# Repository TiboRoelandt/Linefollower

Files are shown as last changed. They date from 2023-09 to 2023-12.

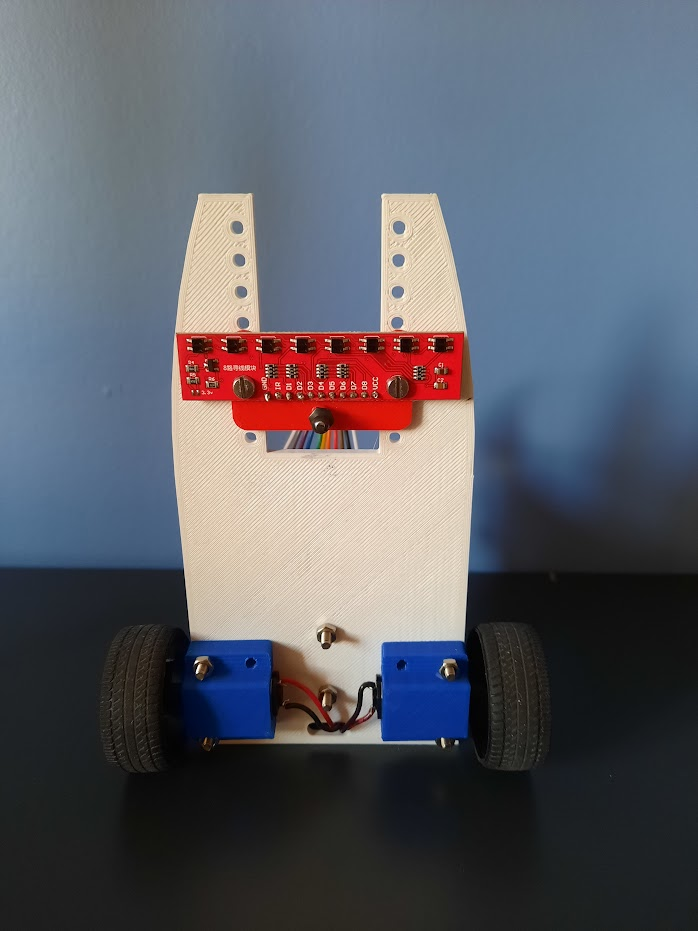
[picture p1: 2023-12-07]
images/LFC2.png

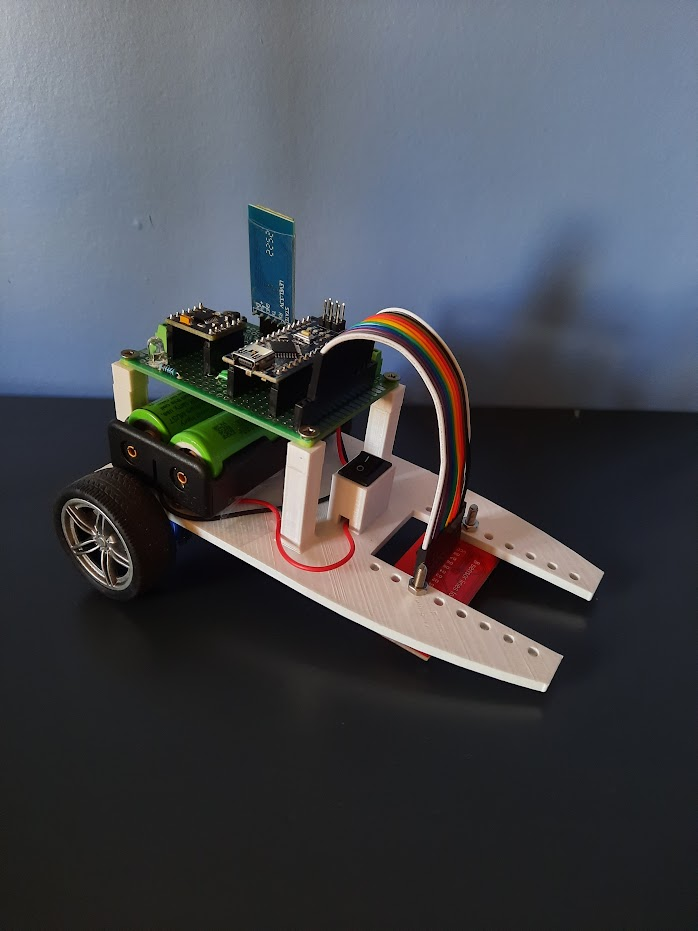
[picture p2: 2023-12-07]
images/LFC1.png

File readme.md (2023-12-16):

# LineFollower

lege repository die je als template kan gebruiken om een eigen repository te starten voor uw linefollower project



## specifications

microcontroller: ATmega328 (Arduino Nano)

motors: Metal Gear motor 6V-50:1

h-bridge: DRV8833

sensors: QTR-8A

batteries: 2x 18650 li-ion

wireless communication: HC-05

distance sensor - motors: 96mm 

weight: 245g

speed: 0,708 m/s

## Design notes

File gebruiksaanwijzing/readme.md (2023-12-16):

# Gebruiksaanwijzing

### opladen / vervangen batterijen
De batterijen die gebruikt worden zijn 2 18650 li-ion batterijen. Deze worden opgeladen met een geschikte oplader. Om de batterijen te vervangen moet eerst de PCB van de auto worden verwijderd. Hierna kunnen de batterijen uit de houder worden gehaald en opgeladen. 

### draadloze communicatie
#### verbinding maken
Voor de draadloze communicatie wordt er gebruik gemaakt van een HC-05 bluetooth module. Op de smartphone wordt de app "Serial Bluetooth Terminal" gebruikt om verbinding te maken met de module. Hiermee kunnen de commando's worden doorgestuurd naar de arduino. 

#### commando's
debug [on/off] => Opvragen van de ingestelde parrameters. 

run  => Starten van de LineFollower. 

stop => Stoppen van de LineFollower.  

set cycle [µs]  => Instellen van de cycle time. Deze is ongeveer het dubbele van de calculation time.

set power [0..255]  => Instellen van de power van de motoren. 

set diff [0..1]  => Door de diff aan te passen zal de auto vertragen of versnellen in de bochten. Hoe hoger diff hoe meer de auto versnelt in de bochten.

set kp [0..] => Dit is de corrigatie van de fout. Hoe hoger kp hoe sterker de auto zich corrigeert om de zwarte lijn in het midden van de sensor te hebben. Als deze te hoog is zal de auto schoken van links naar rechts over de lijn.

set ki [0..] => Hoe langer de error duurt hoe sterker de linfollower zal bijsturen. 

set kd [0..] => Dit is de foutverandering. Deze kijkt naar de fout uit de vorige cyclus en gaat dan de fout bijregelen. Was deze fout groot dan wordt er meer gecorigeerd.

calibrate black => Hierdoor worden de zwarte waarden van de sensor gecalibreert.  

calibrate white => Hierdoor worden de witte waarden van de sensor gecalibreert. 

### kalibratie
Het kalibreren van de senor gebeurd met de commando's "calibrate black" en "calibrate white". Om de zwarte waarden te kalibreren moet de sensor boven een zwart oppervlak staan en dan het commando ingeven. Om de witte waarden te kalibreren gebeurd het zelfde maar op een wit oppervlak. 

### settings
De robot rijdt stabiel met volgende parameters: cycle time: 3000, power: 75, diff: 0.75, kp:18, ki: 0.5, kd:0.4

### start/stop button
Er is een start/stop button voorzien op de robot. Deze bevindt zich op de PCB, de knop is aangesloten op een intterupt pin (pin2). Deze werkt met een intterupt functie en een debounce.

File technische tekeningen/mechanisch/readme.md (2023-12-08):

Assembly:



Base:


Sensor plaatje:



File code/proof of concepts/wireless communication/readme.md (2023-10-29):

# draadloze communicatie proof of concept
minimale hard- en software waarmee aangetoond wordt dat duplex kan gecommuniceerd worden tussen de microcontroller en een smartphone, gebruik makend van Arduino bluetooth controller.
<br />
### configuratie
HC-05
### opmerkingen
App: Arduino bluetooth controller
### gebruiksaanwijzing

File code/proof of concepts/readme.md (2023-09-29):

# Proof of Concepts

Een proof of concept is een combinatie van minimale hard- en software om eenvoudig aan te tonen dat iets werkt.  
Proof of concepts kunnen enerzijds als eerste poging dienen om een bepaald onderdeel van het project werkend te krijgen. Anderzijds kunnen ze tijdens het debuggen van het finale project dienen als test om eventuele hardware problemen te elimineren bij onduidelijke problemen.
<br />  
<br />
Een proof of concept bestaat uit
* een elektronisch schema (indien van toepassing)
* minimale code om de voorop gestelde zaken te demonstreren
* minimale uitleg / aandachtspunten
<br />
De elektronische schakelingen van de proof of concepts komen bij voorkeur overeen met deze van de uiteindelijke linefollower, zodat de code zonder aanpassingen op het finale project kan draaien.

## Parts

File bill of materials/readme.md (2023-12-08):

## bill of materials
<br />

|volgnummer|naam|omschrijving|nieuw/recup|kostprijs/stuk|aantal|subtotaal|
|---|----|---|---|---|---|---|
| 1|  Microcontroller | ATmega328P | Nieuw | €2,61 | 1 | €2,61 |
| 2|  Sensoren  | QTR-8A | Nieuw | €1,24 | 1 | €1,24 |
| 3| H-brug  | DRV8833 | Nieuw | €0,48 | 1 |  €0,48 |
| 4|  Motoren  | Gear motor 6V 50:1 | Nieuw | €3,25 | 2 | €6,5 |
| 5|  Bluetooth  | HC-05 module | Nieuw | €3,90 | 1 | €3,90 |
| 6|  Batterij  | 18650 | Recup | €0 | 1 | €0 |
| 7|  Batterij houder  | 18650 houder | Recup | €0 | 1 | €0 |
| 8|  Batterij oplader  | 18650 oplader | Nieuw | €3,69 | 1 | €3,69 |
| 9|  Weerstanden | 10kΩ & 220Ω | Recup | €0 | 2 | €0 |
| 10|  Led/knop | Led/knop | Recup | €0 | 2 | €0 |
| 11|  Schakelaar | Aan/uit | Nieuw | €0,83 | 1 | €0,83 |
| 12|  Kabels | Kabels | Nieuw | €1,25 | 3 | €1,25 |
| 13|  Printplaaat | Printplaat plan B | Nieuw | €0,80 | 1 | €0,80 |
| 14|  Pinheaders | Pinheaders | Nieuw | €2,22 | 1 | €2,22 |
| 15|  Wielen | Wielen | Nieuw | €3 | 2 | €6 |
| 16|  Frame | PLA | Nieuw | €1 | 1 | €1  |
| | | | | |  Totaal | € 30,52  |

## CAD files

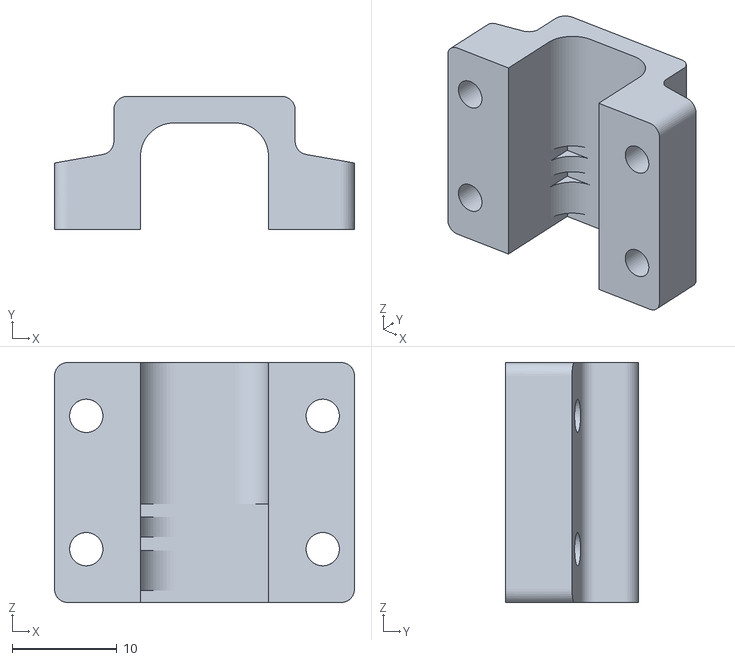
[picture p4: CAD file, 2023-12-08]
technische tekeningen/mechanisch/motor_mount_v2.1.1_straight.STL
28.6 x 12.7 x 22.9

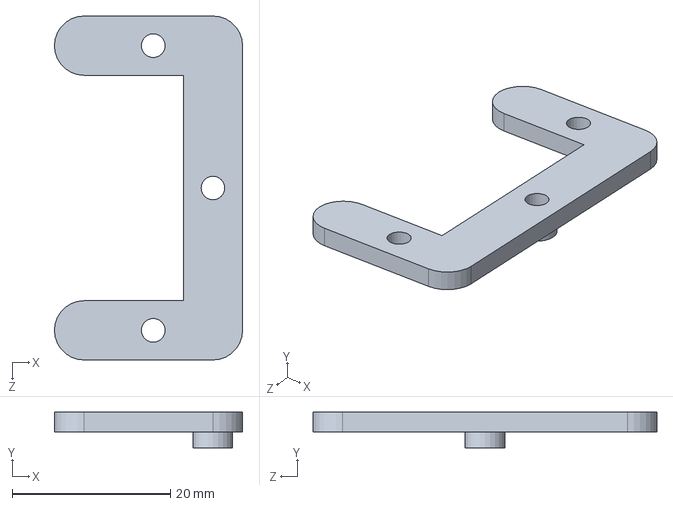
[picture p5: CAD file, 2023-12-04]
technische tekeningen/mechanisch/Sensor plaatje.SLDPRT
23.8 x 4.50 x 43.5 mm

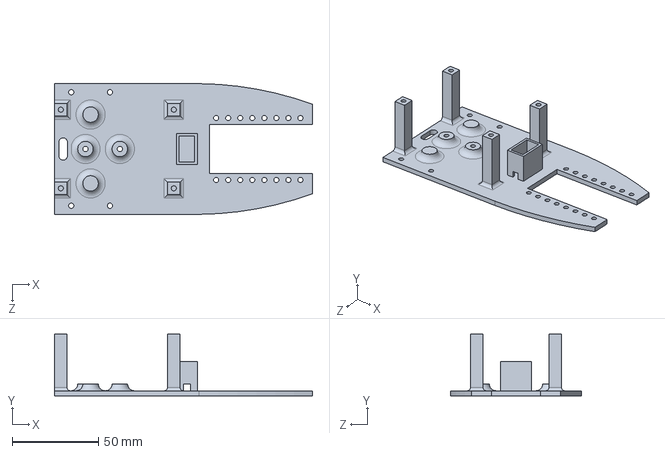
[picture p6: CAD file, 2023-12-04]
technische tekeningen/mechanisch/Base.SLDPRT
150.0 x 36.0 x 76.0 mm

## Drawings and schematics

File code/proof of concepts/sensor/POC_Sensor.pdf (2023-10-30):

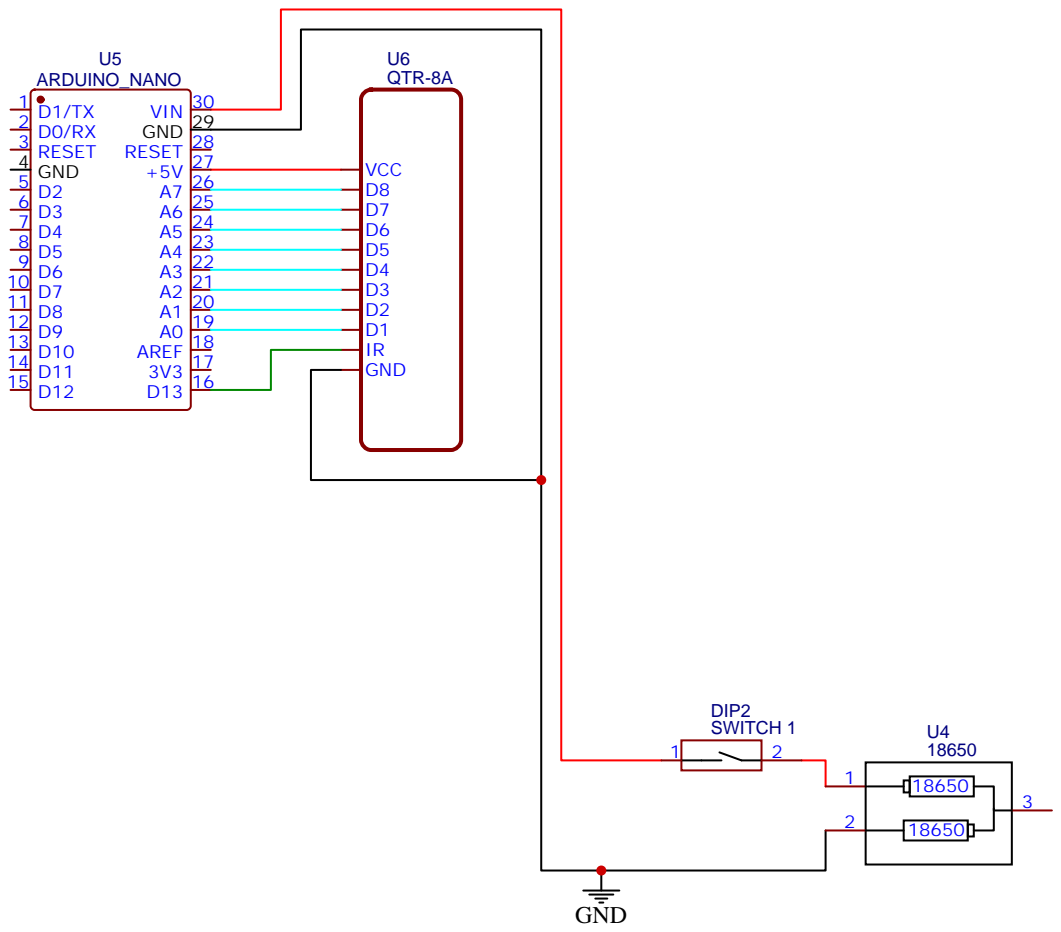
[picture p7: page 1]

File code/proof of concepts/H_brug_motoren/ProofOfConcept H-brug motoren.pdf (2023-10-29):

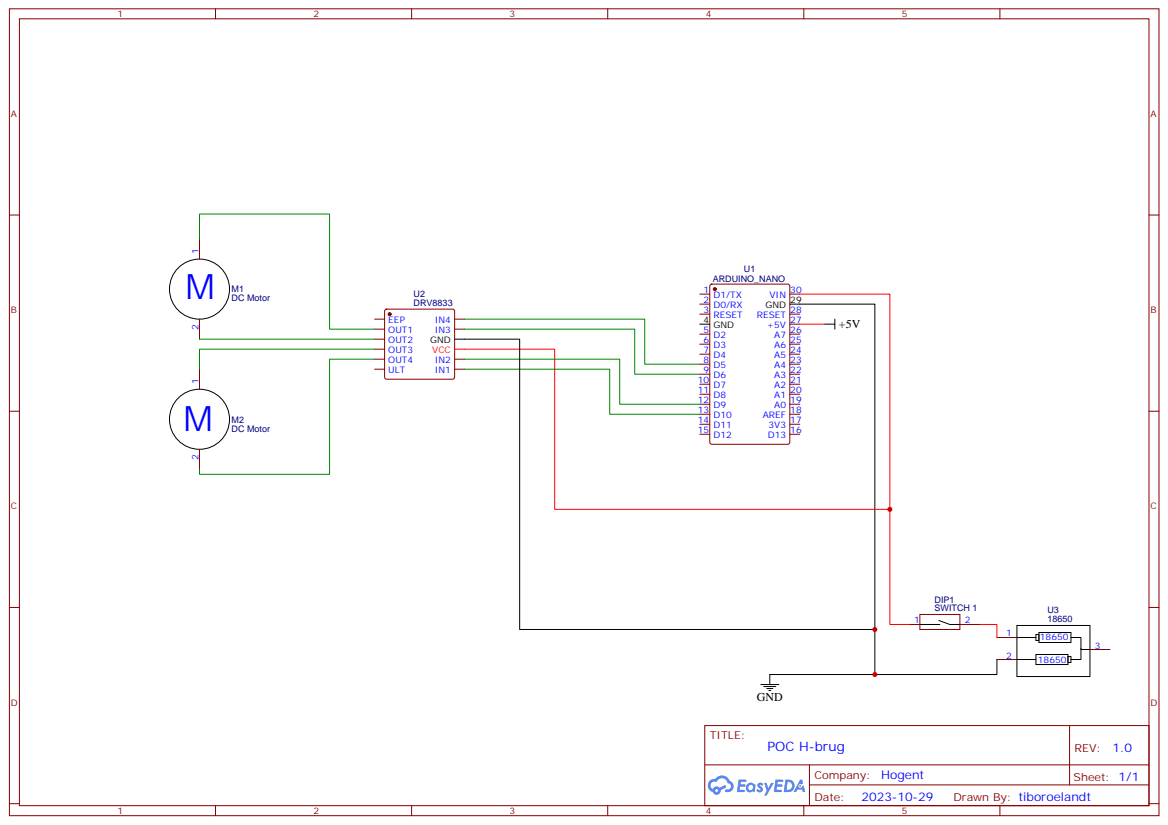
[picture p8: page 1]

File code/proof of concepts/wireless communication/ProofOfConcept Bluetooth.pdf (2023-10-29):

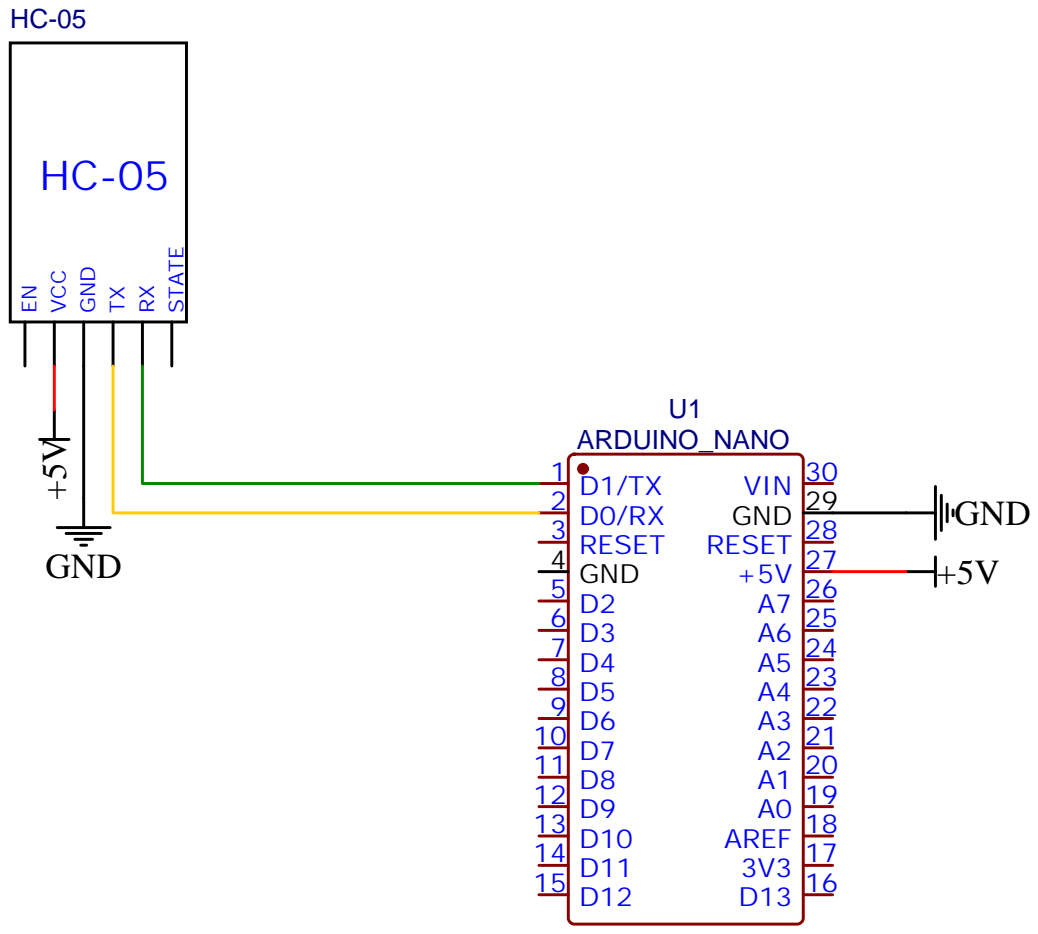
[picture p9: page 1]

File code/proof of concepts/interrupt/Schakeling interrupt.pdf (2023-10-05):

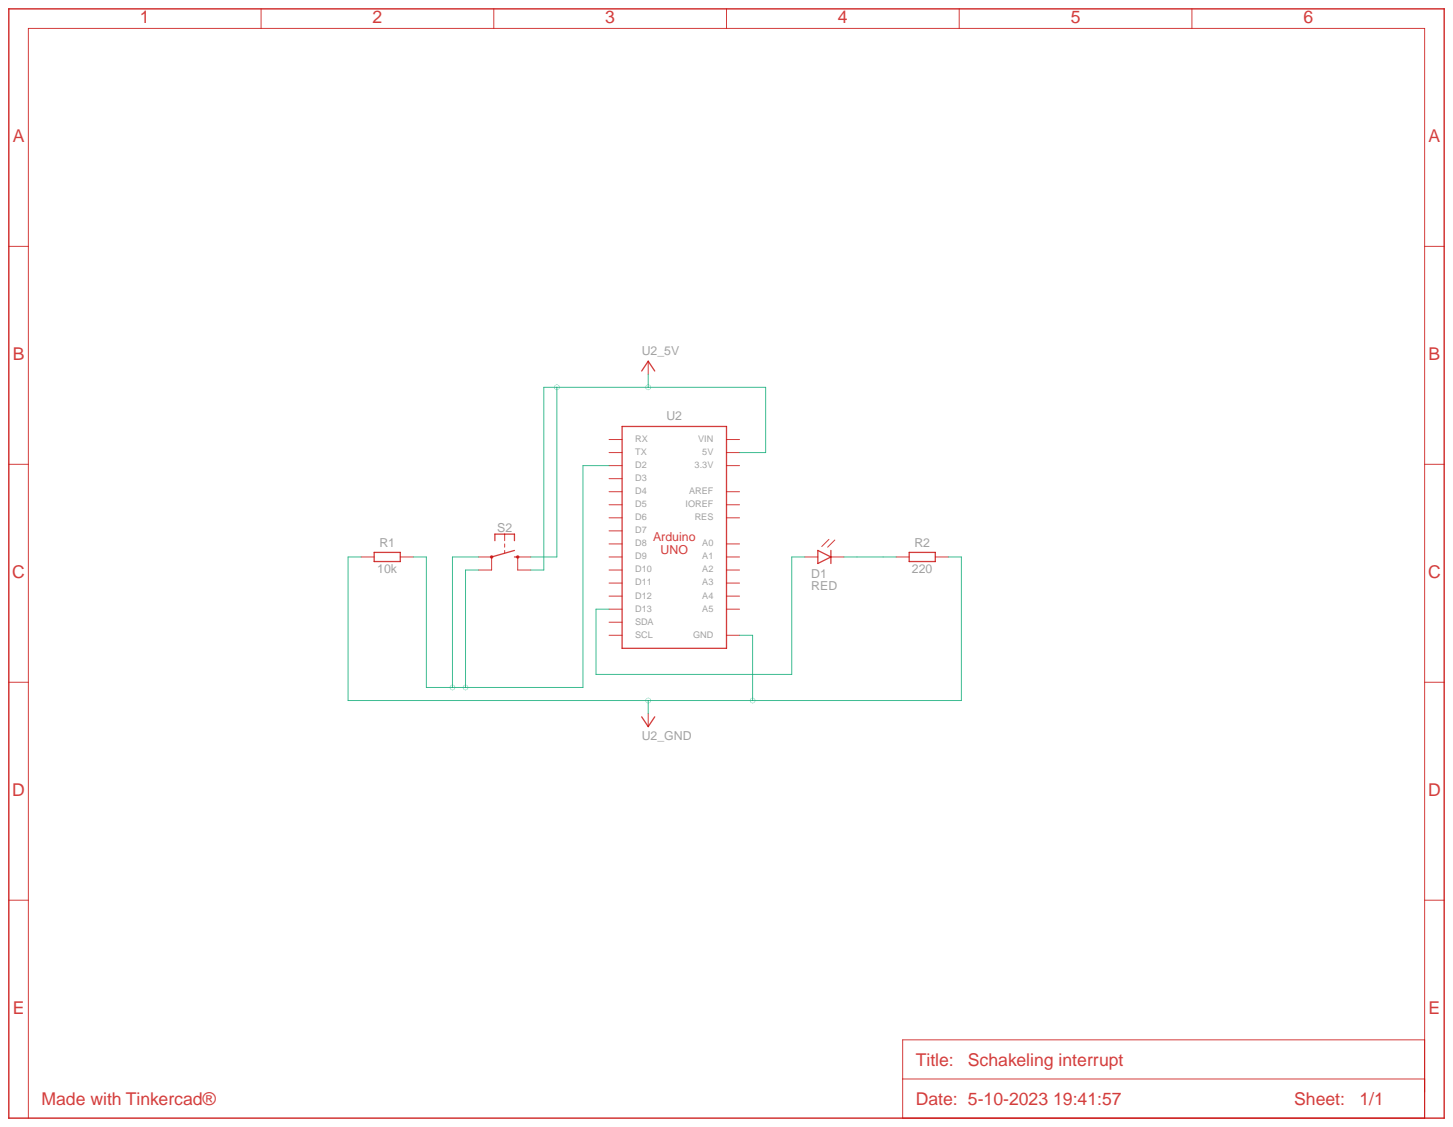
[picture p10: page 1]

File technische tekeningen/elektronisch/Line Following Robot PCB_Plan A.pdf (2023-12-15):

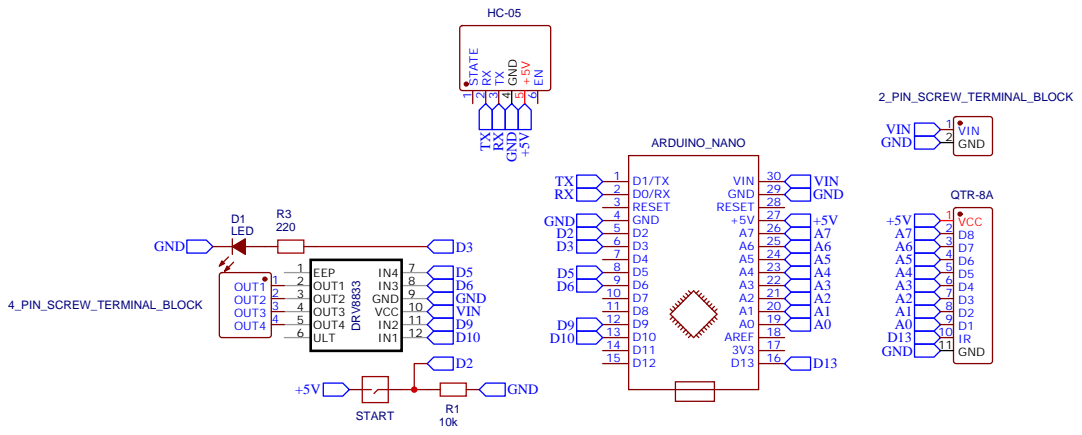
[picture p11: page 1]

Drawn By: Tibo Roelandt

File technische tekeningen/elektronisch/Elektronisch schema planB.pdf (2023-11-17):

HC-05

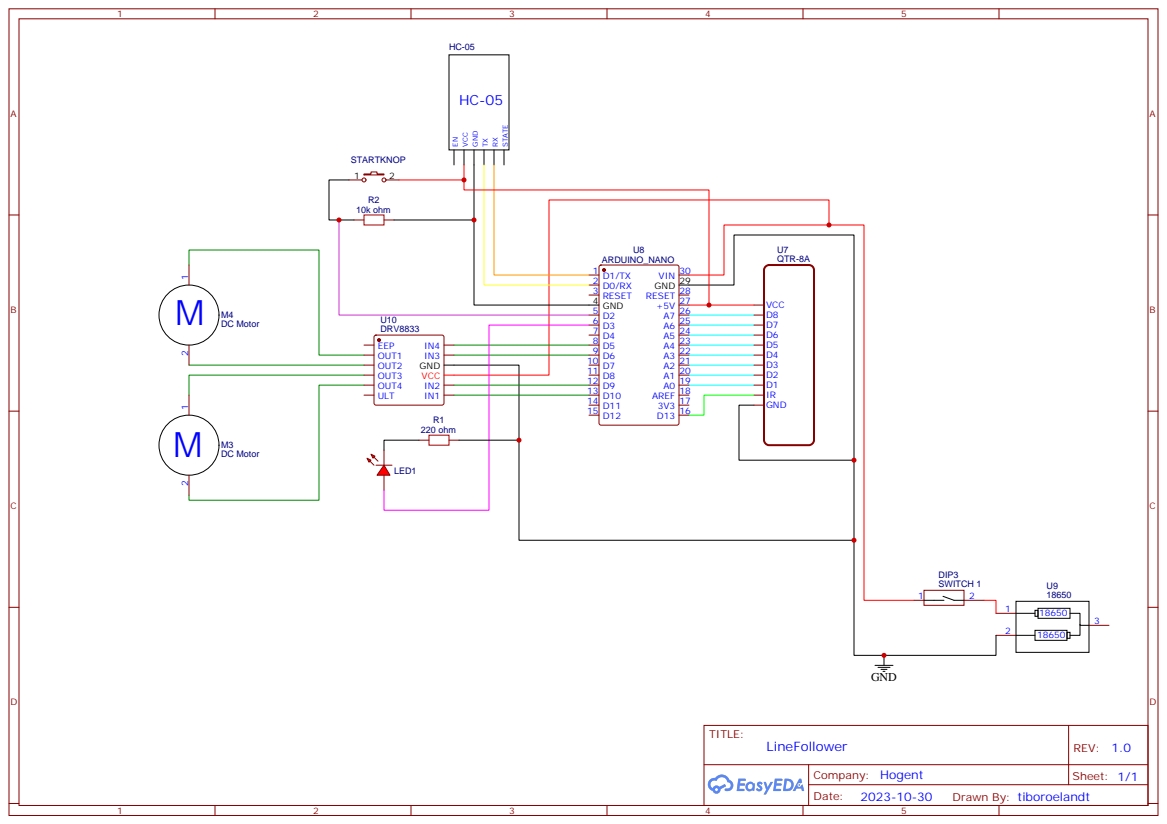
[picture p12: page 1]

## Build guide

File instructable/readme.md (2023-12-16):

# Instructable

Een instructable is een stappenplan - zonder verdere uitleg - hoe je vertrekkend van de bill of materials en gebruik makend van de technische tekeningen de robot kan nabouwen. Ook de nodige stappen om de microcontroller te compileren en te uploaden staan beschreven.  

### stap 1
bestel alle componenten uit de bill of materials  

### stap 2
Test aan de hand van de proof of concepts alle componenten. 
Indien nodig kan je de datasheets raadplegen

### stap 3
Nu gaan we de printplaat solderen. Doe dit met behulp van het elektronisch schema. 



### stap 4
Het chassis kan je 3D printen. De bestanden hiervoor vind je terug onder technische tekeningen => mechanisch.
De wielen zijn aangekocht die passen op de metal gear motoren.

### stap 5
Om alles te monteren heb je M3-boutjes nodig.
Eerst worden de motoren met de motor mounts vastgezet. Hierna wordt de batterij houder gemonteerd. Soldeer de schakelaar tussen de voeding van de batterijen. 
Het monteren van de printplaat gebeurd rechtstreeks op het ge-3Dprinte chassis.
Plaats de sensor ongveer in het midden van de rij gaatjes die hiervoor voorzien zijn. Later kan je dan de afstand van de sensor ten opzichte van de wielen nog aanpassen om jouw linefollower te optimaliseren. 

### stap 6
Upload het programma naar jouw arduino nano. Het programma kan je vinden onder code => finaal. Let er op dat de HC-05 module tijdens het uploaden niet verbonden is met de arduino. 

### stap 7
Het instellen van de parrameters gebeurd via bluetooth en de app "Serial Bluetooth Terminal" op de smartphone. De parrameters die ik gebruikt heb zijn terug te vinden bij gebruiksaanwijzing => setting. 

Als je al bovenstaande stappen hebt volbracht is jouw auto klaar voor gebruik. 


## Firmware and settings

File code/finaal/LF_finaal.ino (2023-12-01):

#include "SerialCommand.h"
#include "EEPROMAnything.h"

#define SerialPort Serial
#define Baudrate 9600

#define MotorLeftForward 5
#define MotorLeftBackward 6
#define MotorRightForward 9
#define MotorRightBackward 10


const int Drukknop = 2;//interupt
const int LED = 3; //Led
const int IR =13; //SensorLED

//interupt:
volatile bool runState = false;
volatile unsigned long lastDebounceTime = 0;  // Tijd voor debouncing
unsigned long debounceDelay = 50;  // Debounce-tijd in milliseconden


SerialCommand sCmd(SerialPort);
bool debug;
bool run;                   
unsigned long previous, calculationTime;


const int sensor[] = {22, 19, A5, A4, A3, A2, A1, A0};


struct param_t
{
  unsigned long cycleTime;
  int black[8];
  int white[8];
  float diff;
  float kp;
  int power;
  float ki;
  float kd;

} params;

int normalised[8];
float debugposition;
float output;
float error;
float iTerm = 0;
float lastErr;


void setup()
{

  pinMode(10, OUTPUT);
  pinMode(9, OUTPUT);
  pinMode(6, OUTPUT);
  pinMode(5, OUTPUT); 

  SerialPort.begin(Baudrate);

  sCmd.addCommand("set", onSet);
  sCmd.addCommand("debug", onDebug);
  sCmd.addCommand("calibrate", onCalibrate);
  sCmd.addCommand("run", onRun);
  sCmd.addCommand("stop", onStop);
  sCmd.setDefaultHandler(onUnknownCommand);

  EEPROM_readAnything(0, params);
  SerialPort.println("ready");

  //Interupt
  pinMode(Drukknop, INPUT);
  attachInterrupt(digitalPinToInterrupt(Drukknop), Interrupt, RISING);

  pinMode(LED, OUTPUT);

  pinMode(IR, OUTPUT);
  digitalWrite(IR, HIGH);
}


void loop()
{
  sCmd.readSerial();
 
  unsigned long current = micros();
  if (current - previous >= params.cycleTime)
  {
    previous = current;
    //normalize
    for (int i = 0; i < 8; i++)
    {
      normalised[i] = map(analogRead(sensor[i]), params.black[i], params.white[i], 0, 1000);
      
    }

    //interpolatie
    int index = 0;
    float position;

    for (int i = 1; i < 8; i++) if (normalised[i] < normalised[index]) index = i;

    if (normalised[index] > 1200) run = false;
    

    if (index == 0) position = -30;
    else if (index == 7) position = 30;
    else
    {
      int sNul = normalised[index];
      int sMinEen = normalised[index-1];
      int sPlusEen = normalised[index+1];

      float b = sPlusEen - sMinEen;
      b = b / 2;

      float a = sPlusEen - b - sNul;

      position = -b / (2 * a);
      position += index;
      position -= 3.5;

      position *= 9.525; //afstand sensoren uit elkaar waarschijnlijk aanpassen

    }
    
    debugposition = position;
    
    //P-regelaar
    error = -position;
    output = error * params.kp;

    //I-Regelaar
    iTerm += params.ki * error;
    iTerm = constrain(iTerm, -510, 510);
    output += iTerm;

    //D-Regelaar
    output += params.kd * (error - lastErr);
    lastErr = error;

    output = constrain(output, -510, 510);

    int powerLeft = 0;
    int powerRight = 0;


    if (run) if (output >= 0)
    {
      powerLeft = constrain(params.power + params.diff * output, -255, 255);
      powerRight = constrain(powerLeft - output, -255, 255);
      powerLeft = powerRight + output;
    }
    else
    {
      powerRight = constrain(params.power - params.diff * output, -255, 255);
      powerLeft = constrain(powerRight + output, -255, 255);
      powerRight = powerLeft - output;
        
    }

    analogWrite(MotorLeftForward, powerLeft > 0 ? powerLeft : 0);
    analogWrite(MotorLeftBackward, powerLeft < 0 ? -powerLeft : 0);
    analogWrite(MotorRightForward, powerRight > 0 ? powerRight : 0);
    analogWrite(MotorRightBackward, powerRight < 0 ? -powerRight : 0);
  }
  
  unsigned long difference = micros() - current;
  if (difference > calculationTime) calculationTime = difference;

}

void onUnknownCommand(char *command)
{
  SerialPort.print("unknown command: \"");
  SerialPort.print(command);
  SerialPort.println("\"");
}


void onSet()
{
  char* param = sCmd.next();
  char* value = sCmd.next();  
  
  if (strcmp(param, "cycle") == 0)
  {
    long newCycleTime = atol(value);
    float ratio = ((float) newCycleTime) / ((float) params.cycleTime);

    params.ki *= ratio;
    params.kd /= ratio;

    params.cycleTime = newCycleTime;
  }

  else if (strcmp(param, "ki") == 0)
  {
    float cycleTimeInSec = ((float) params.cycleTime) / 1000000;
    params.ki = atof(value) * cycleTimeInSec;
  }

  else if (strcmp(param, "kd") == 0)
  {
    float cycleTimeInSec = ((float) params.cycleTime) / 1000000;
    params.kd = atof(value) / cycleTimeInSec;
  }

  else if (strcmp(param, "power") == 0) params.power = atol(value);
  else if (strcmp(param, "diff") == 0) params.diff = atof(value);
  else if (strcmp(param, "kp") == 0) params.kp = atof(value);

  EEPROM_writeAnything(0, params);
}

void onDebug()
{
  SerialPort.print("cycle time: ");
  SerialPort.println(params.cycleTime);
  
  /* parameters weergeven met behulp van het debug commando doe je hier ... */
  SerialPort.print("black: ");
  for (int i = 0; i < 8; i++)
  {
    SerialPort.print(params.black[i]);
    SerialPort.print(" ");
  }
  SerialPort.println(" ");

  SerialPort.print("white: ");
  for (int i = 0; i < 8; i++)
  {
    SerialPort.print(params.white[i]);
    SerialPort.print(" ");
  }
  SerialPort.println(" ");

  SerialPort.print("Normalised: ");
  for (int i = 0; i < 8; i++)
  {
    SerialPort.print(normalised[i]);
    SerialPort.print(" ");
  }
  SerialPort.println(" ");

  SerialPort.print("position: ");
  SerialPort.println(debugposition);

  SerialPort.print("Power: ");
  SerialPort.println(params.power);

  SerialPort.print("diff: ");
  SerialPort.println(params.diff);

  SerialPort.print("kp: ");
  SerialPort.println(params.kp);

  float cycleTimeInSec = ((float) params.cycleTime) / 1000000;
  float ki = params.ki / cycleTimeInSec;
  SerialPort.print("Ki: ");
  SerialPort.println(ki);

  float kd = params.kd * cycleTimeInSec;
  SerialPort.print("Kd: ");
  SerialPort.println(kd);

  SerialPort.print("RUN: ");
  SerialPort.println(params.kp);
  
  SerialPort.println(" ");
  SerialPort.print("calculation time: ");
  SerialPort.println(calculationTime);
  calculationTime = 0;
}

void onCalibrate()
{
  char* param = sCmd.next();

  if (strcmp(param, "black") == 0)
  {
    SerialPort.print("start calibrating black...");
    for (int i = 0; i < 8; i++) params.black[i] = analogRead(sensor[i]);
    SerialPort.println("done");
  }
  else if (strcmp(param, "white") == 0)
  {
    SerialPort.print("start calibrating white...");
    for (int i =0; i < 8; i++) params.white[i] = analogRead(sensor[i]);
    SerialPort.println("done");
  }

  EEPROM_writeAnything(0, params);
}

void onRun()
{
  run = true;
  digitalWrite(LED, HIGH);
}

void onStop()
{
  run = false;
  digitalWrite(LED, LOW);
}

void Interrupt()
{
  // Lees de status van de drukknop
  int buttonState = digitalRead(Drukknop);

  // Debounce de drukknop met millis
  if ((millis() - lastDebounceTime) > debounceDelay) {
    // Als de knop opgaand is, wissel de status van de LED
    if (buttonState == HIGH) {
      runState = !runState;

      // Schakel de LED in of uit op basis van de nieuwe status
      digitalWrite(LED, runState);
      run = runState;
      iTerm = 0;
    }

    // Update de tijd van de laatste debouncing
    lastDebounceTime = millis();
  }
  
}

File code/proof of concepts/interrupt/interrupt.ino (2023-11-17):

const int buttonPin = 2;   // Druknop op pin 2
const int ledPin = 3;      // LED op pin 3

volatile bool ledState = false;  // Huidige status van de LED
volatile unsigned long lastDebounceTime = 0;  // Tijd voor debouncing
unsigned long debounceDelay = 50;  // Debounce-tijd in milliseconden

void setup() {
  pinMode(buttonPin, INPUT);  // Configureer pin 2 als ingang met pull-up weerstand
  pinMode(ledPin, OUTPUT);           // Configureer pin 3 als uitgang

  attachInterrupt(digitalPinToInterrupt(buttonPin), buttonInterrupt, RISING);  // Koppel de interrupt-functie aan de opgaande flank van de drukknop
}

void loop() {
  // Doe hier andere taken die onafhankelijk zijn van de drukknopstatus
}

void buttonInterrupt() {
  // Lees de status van de drukknop
  int buttonState = digitalRead(buttonPin);

  // Debounce de drukknop met millis
  if ((millis() - lastDebounceTime) > debounceDelay) {
    // Als de knop opgaand is, wissel de status van de LED
    if (buttonState == HIGH) {
      ledState = !ledState;

      // Schakel de LED in of uit op basis van de nieuwe status
      digitalWrite(ledPin, ledState);
    }

    // Update de tijd van de laatste debouncing
    lastDebounceTime = millis();
  }
}
